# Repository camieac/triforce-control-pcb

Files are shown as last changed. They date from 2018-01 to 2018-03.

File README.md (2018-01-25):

# triforce-control-pcb

## Repository Navigation
This repository hosts the electronics hardware designs for the Triforce Fight Controller. Links to the main software repositories are below:

### [Triforce Control](https://github.com/TeamTriforceUK/triforce-control)

The Triforce Control firmware (mbed OS) runs on an LPC1768 (ARM Cortex M3). The firmware is responsible for controlling the robot.

### [Triforce Telemetry](https://github.com/TeamTriforceUK/triforce-telemetry)

The Triforce Telemetry repository hosts firmware (FreeRTOS) for the ESP8266 WiFi chip. This microcontroller works alongside the mbed to provide telemetry functionality via an HTTP server.

The ESP8266 allows us to communicate telemetry from Triforce to connected mobile devices (tablets, laptops, mobile phones). We also control non-safety critical settings such as LED lights from the mobile device.

## System Overview

### Microprocessors

| Device  | Firmware  | Language |
|---|---|---|
| [LPC1768](https://developer.mbed.org/platforms/mbed-LPC1768/) | [mbed OS](https://www.mbed.com/en/development/mbed-os/) | C++ |
| [ESP8266](https://www.adafruit.com/product/2471) | [FreeRTOS](http://www.freertos.org/)  | C |

### Sensors

| Sensor | Purpose | Communication |
|---|---|---|
| [BNO055](https://learn.adafruit.com/adafruit-bno055-absolute-orientation-sensor/overview) | Orientation, direction, acceleration |  I2C |

# PCB Spec

# Board Dimensions

| Width | Height | Thickness |
|---|---|---|
| 75mm  | 85mm | 1.6mm |

# Useful Links

## Enclosure

https://www.hammfg.com/files/parts/pdf/1455J1202.pdf
https://www.hammfg.com/part/1455J1202

## Generating gerber files

http://support.seeedstudio.com/knowledgebase/articles/1824574-how-to-generate-gerber-and-drill-files-from-kicad

## Contributing

We are open to any contributions in terms of ideas, suggestions, bug reports, development. Feel free to open GitHub issues regarding any contributions.

## Licensing

Licensed under CERN OHL v.1.2.

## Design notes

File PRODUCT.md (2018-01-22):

# PRODUCT.TXT

This file lists all known Triforce Fight Controller products that have been manufactured to date.
We are always interested in seeing our work being used by others.
We invite anyone who has made any of our boards to let us know and we will gladly add you to this list.

| Name | Team | Date (ISO 8601) | Version | Repository | Commit | Quantity | Purpose | Manufacturer |
|---|---|---|---|---|---|---|---|---|
| Cameron Craig | Team Triforce | 2018-01-19 | pre-release | github.com/camieac/triforce-control-pcb  | aeb3d275cbf074ca4e43f0d91900493fc6915f59 | 10 | Prototype | PCBWay |

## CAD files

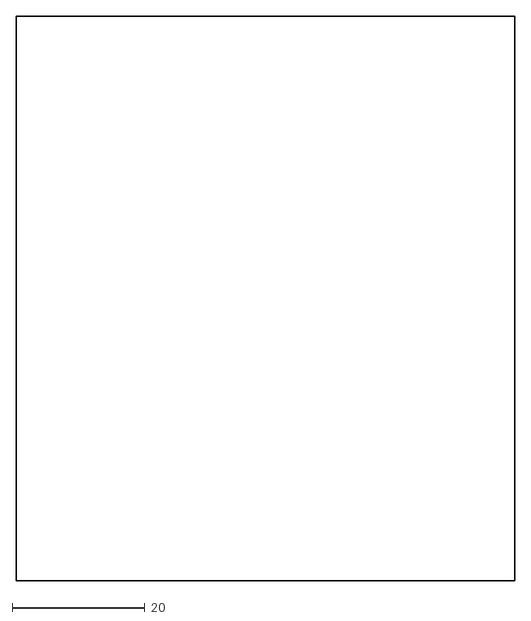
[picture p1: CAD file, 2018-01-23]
3d/drawings/board_outline2.dxf
75.0 x 85.0

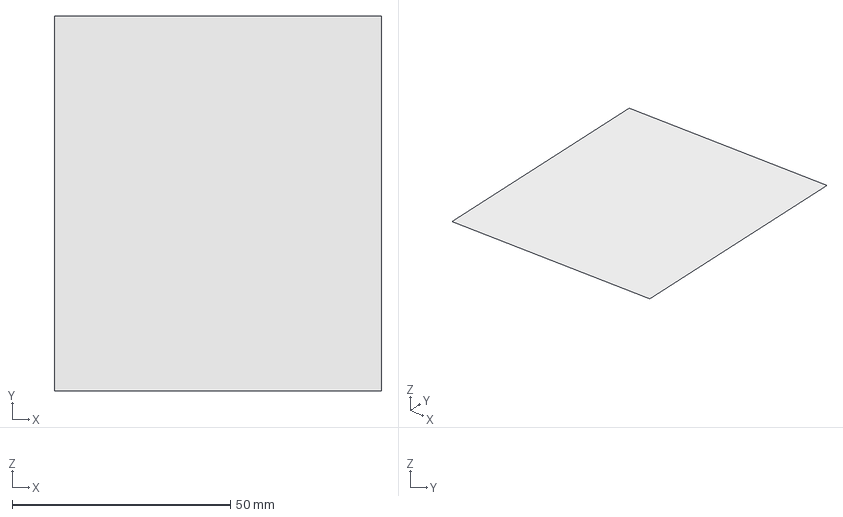
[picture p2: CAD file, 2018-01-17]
3d/drawings/board_outline.fcstd
75.0 x 86.0 x 0 mm

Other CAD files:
3d/drawings/board_outline.dxf

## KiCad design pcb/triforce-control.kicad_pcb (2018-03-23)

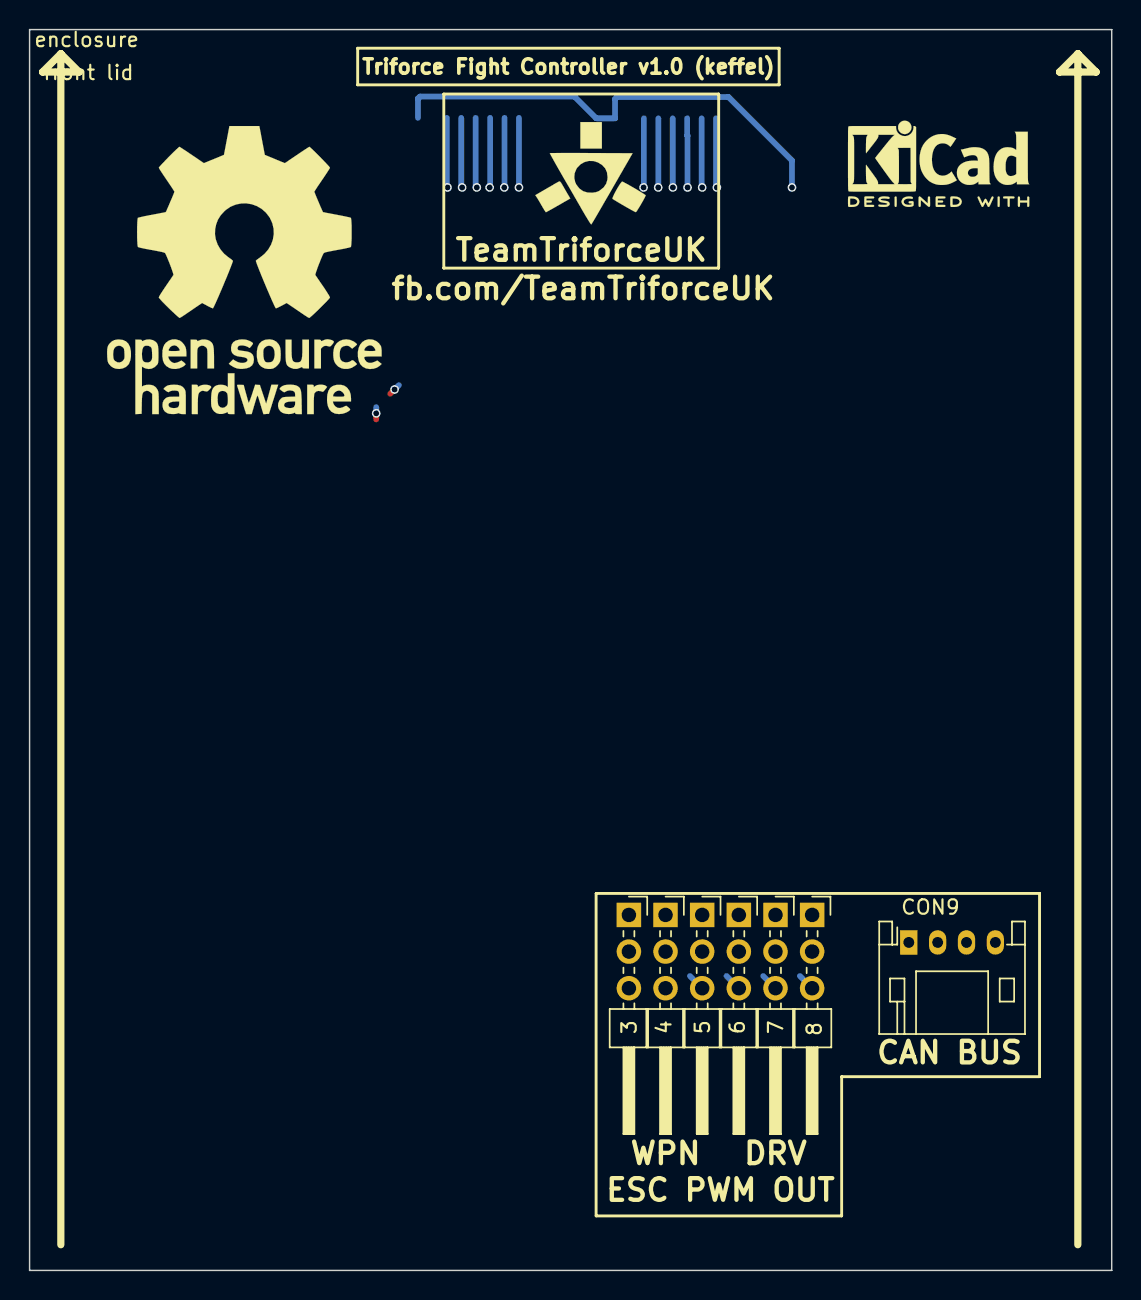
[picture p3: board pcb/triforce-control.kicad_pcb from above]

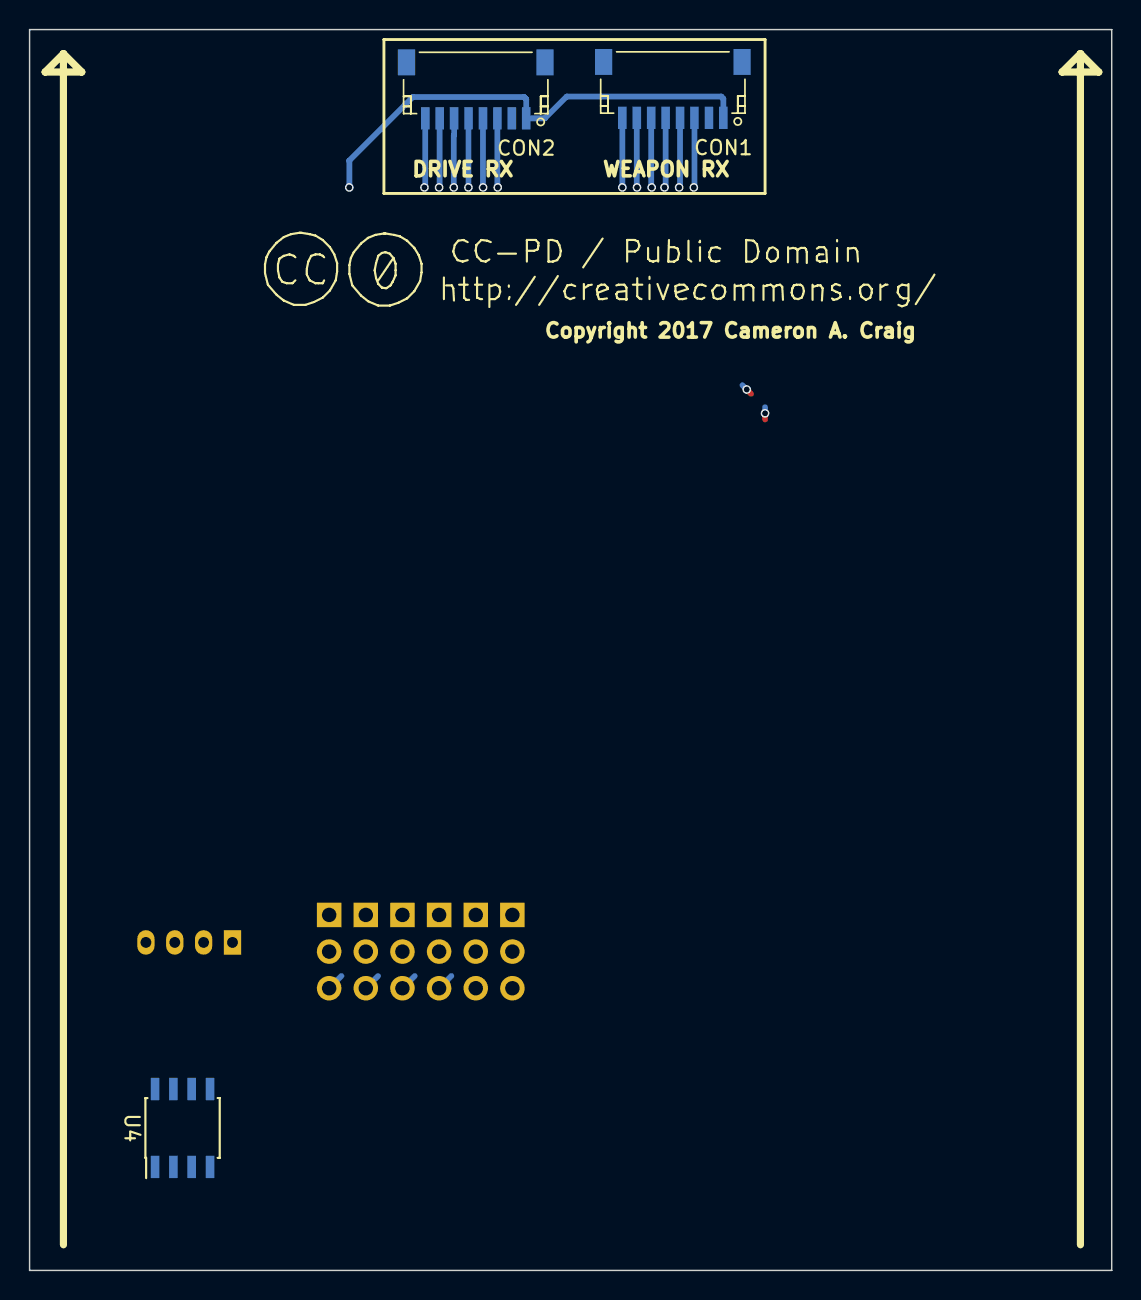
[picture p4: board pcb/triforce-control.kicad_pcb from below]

Board: 2 copper layers, 75.0 x 86.0 mm, 13 parts (3 on the bottom side), 4 nets.

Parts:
3: CON_ESC_W1; Pin_Header_Angled_3x01_Pitch2.54mm
4: CON_ESC_W2; Pin_Header_Angled_3x01_Pitch2.54mm
5: CON_ESC_W3; Pin_Header_Angled_3x01_Pitch2.54mm
6: CON_ESC_D1; Pin_Header_Angled_3x01_Pitch2.54mm
7: CON_ESC_D2; Pin_Header_Angled_3x01_Pitch2.54mm
8: CON_ESC_D3; Pin_Header_Angled_3x01_Pitch2.54mm
CON1, CON2: Conn_01x08; JST_SH_SM08B-SRSS-TB_08x1.00mm_Angled
CON9: Conn_01x04; JST_PH_S4B-PH-K_04x2.00mm_Angled
U4: SN65HVD232; SOIC-8_3.9x4.9mm_Pitch1.27mm
back lid: enclosure
enclosure: enclosure
front lid: enclosure

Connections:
+5V: 3.2, 4.2, 5.2, 6.2, 7.2, 8.2, CON1.2, CON2.2, CON9.4
CAN_H: CON9.3, U4.7
CAN_L: CON9.2, U4.6
GND: 3.1, 4.1, 5.1, 6.1, 7.1, 8.1, CON1.1, CON2.1, CON9.1, U4.2

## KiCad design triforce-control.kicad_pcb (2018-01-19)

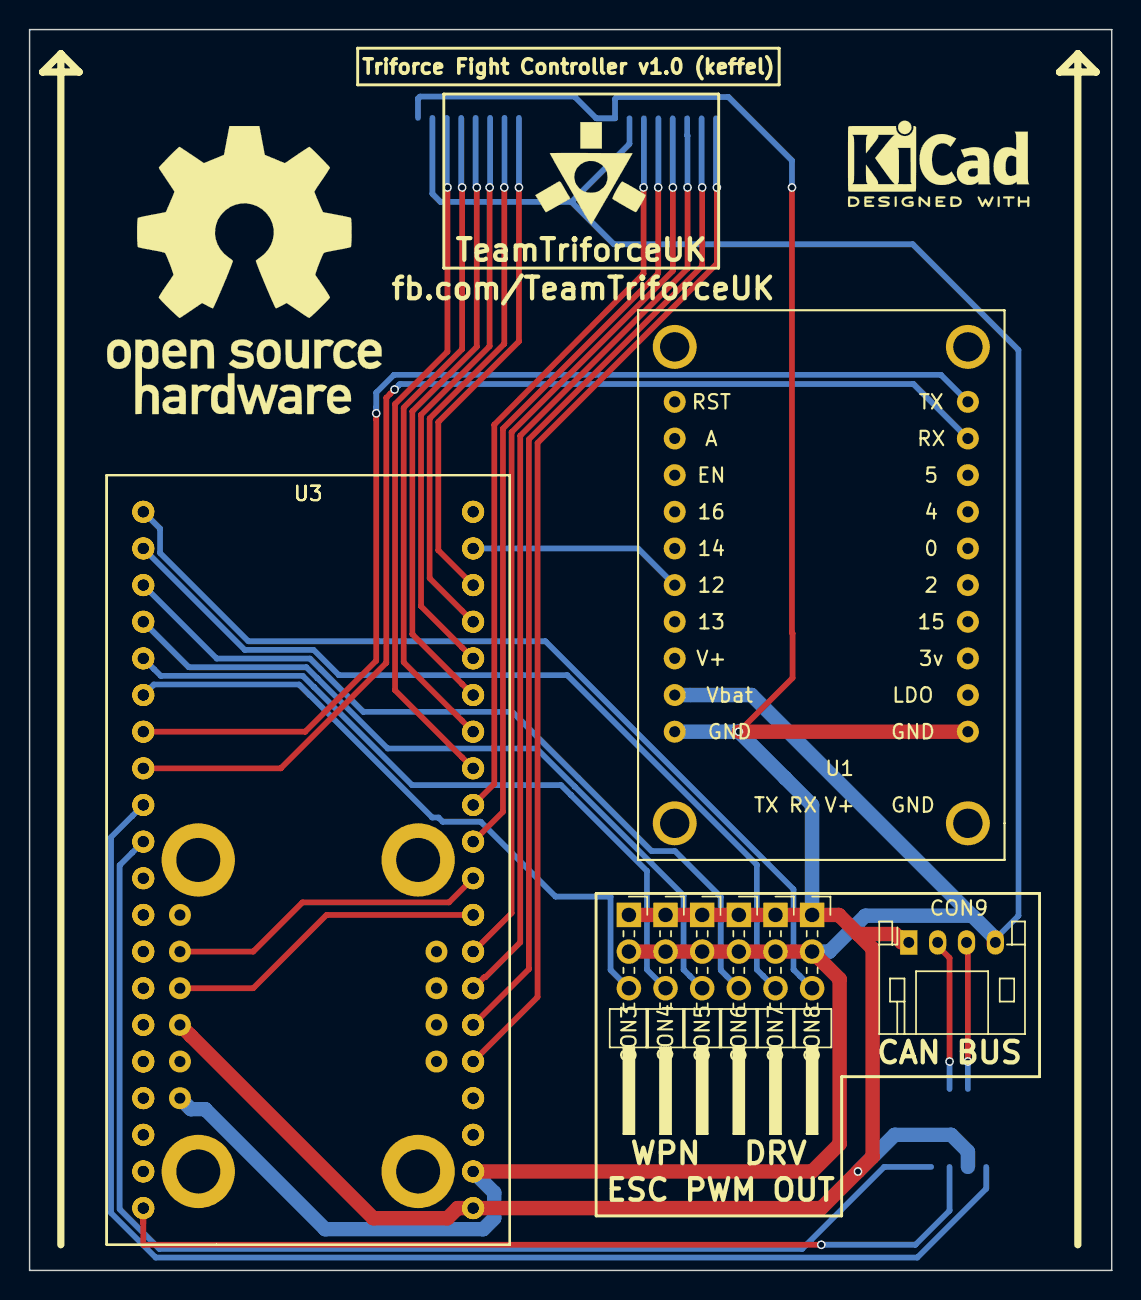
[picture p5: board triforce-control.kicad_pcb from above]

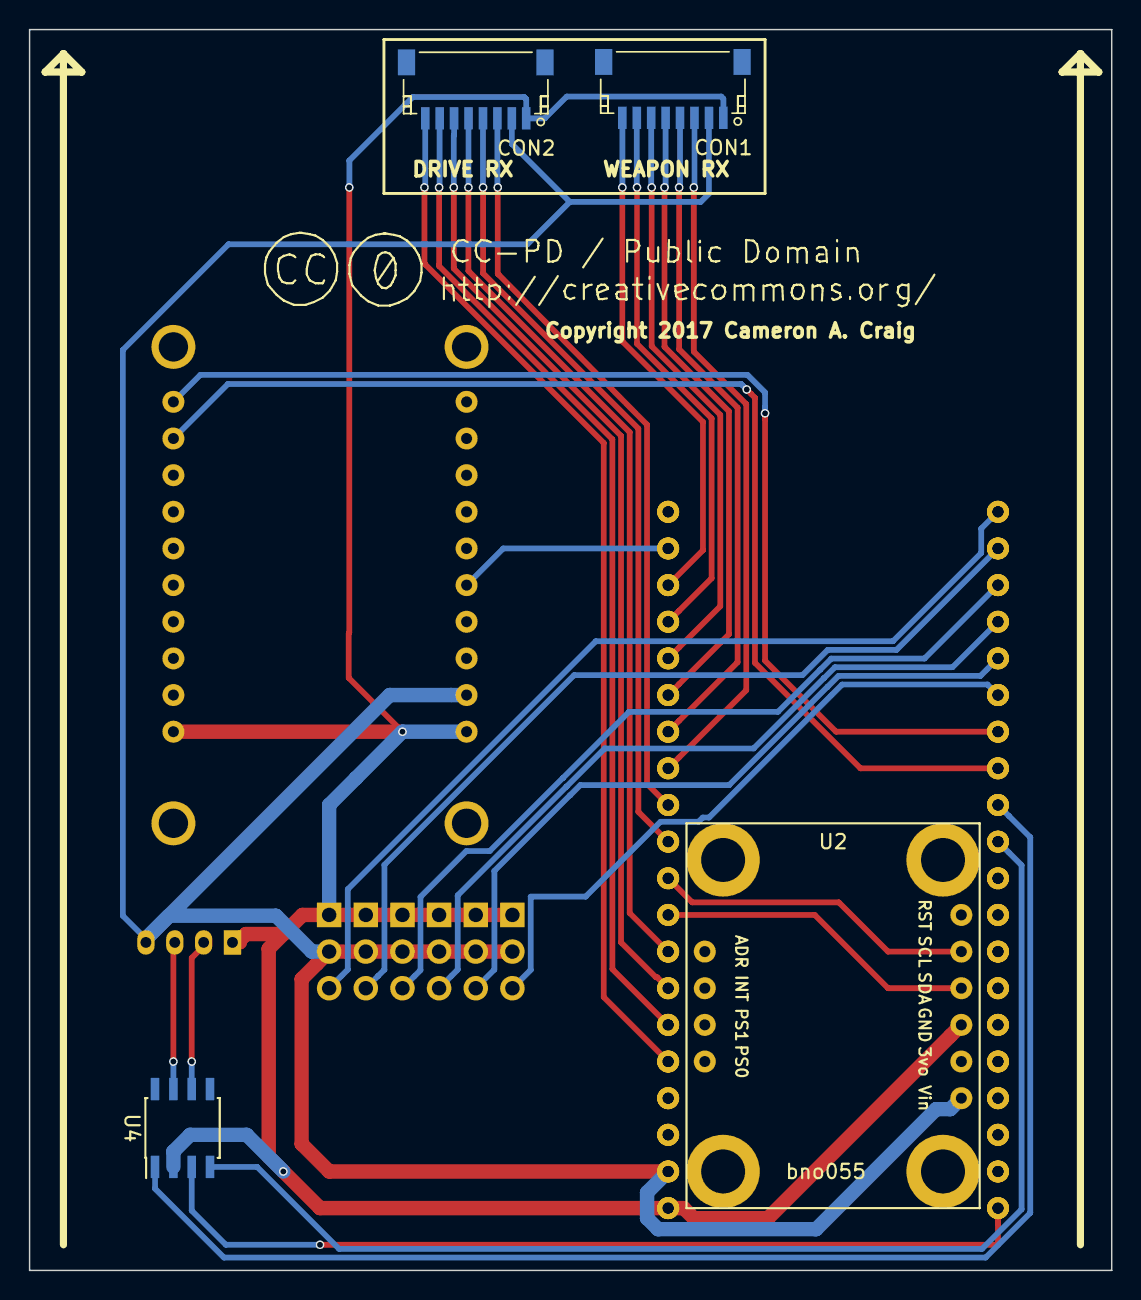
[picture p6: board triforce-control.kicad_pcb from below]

Board: 2 copper layers, 75.0 x 86.0 mm, 14 parts (4 on the bottom side), 42 nets.

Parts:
CON1, CON2: Conn_01x08; JST_SH_SM08B-SRSS-TB_08x1.00mm_Angled
CON3: CON_ESC_W1; Pin_Header_Angled_3x01_Pitch2.54mm
CON4: CON_ESC_W2; Pin_Header_Angled_3x01_Pitch2.54mm
CON5: CON_ESC_W3; Pin_Header_Angled_3x01_Pitch2.54mm
CON6: CON_ESC_D1; Pin_Header_Angled_3x01_Pitch2.54mm
CON7: CON_ESC_D2; Pin_Header_Angled_3x01_Pitch2.54mm
CON8: CON_ESC_D3; Pin_Header_Angled_3x01_Pitch2.54mm
CON9: Conn_01x04; JST_PH_S4B-PH-K_04x2.00mm_Angled
U1: ADAFRUIT_HUZZAH; ESP8266
U2: bno055; BNO055
U3, U3#2: LPC1768; lpc1768
U4: SN65HVD232; SOIC-8_3.9x4.9mm_Pitch1.27mm

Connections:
+5V: CON1.2, CON2.2, CON3.2, CON4.2, CON5.2, CON6.2, CON7.2, CON8.2, CON9.4, U1.9, U2.1, U3.2, U3#2.2
BNO_MBED_SCL: U2.5, U3.10, U3#2.10
BNO_MBED_SDA: U2.4, U3.9, U3#2.9
CAN_H: CON9.3, U4.7
CAN_L: CON9.2, U4.6
CAN_RXD: U3.30, U3#2.30, U4.4
CAN_TXD: U3.29, U3#2.29, U4.1
ESP_MBED_RX: U1.20, U3.27, U3#2.27
ESP_MBED_TX: U1.19, U3.28, U3#2.28
ESP_READY: U1.6, U3.19, U3#2.19
GND: CON1.1, CON2.1, CON3.1, CON4.1, CON5.1, CON6.1, CON7.1, CON8.1, CON9.1, U1.10, U1.11, U2.3, U3.1, U3#2.1, U4.2
IN_RX_D1: CON1.3, U3.13, U3#2.13
IN_RX_D2: CON1.4, U3.14, U3#2.14
IN_RX_D3: CON1.5, U3.15, U3#2.15
IN_RX_D4: CON1.6, U3.16, U3#2.16
IN_RX_D5: CON1.7, U3.17, U3#2.17
IN_RX_D6: CON1.8, U3.18, U3#2.18
IN_RX_W1: CON2.3, U3.12, U3#2.12
IN_RX_W2: CON2.4, U3.11, U3#2.11
IN_RX_W3: CON2.5, U3.8, U3#2.8
IN_RX_W4: CON2.6, U3.7, U3#2.7
IN_RX_W5: CON2.7, U3.6, U3#2.6
IN_RX_W6: CON2.8, U3.5, U3#2.5
MBED_3V3: U3.40, U3#2.40, U4.3
unnamed: U3.3, U3#2.3
unnamed: U3.4, U3#2.4
unnamed: U3.20, U3#2.20
unnamed: U3.31, U3#2.31
unnamed: U3.32, U3#2.32
unnamed: U3.33, U3#2.33
unnamed: U3.34, U3#2.34
unnamed: U3.35, U3#2.35
unnamed: U3.36, U3#2.36
unnamed: U3.37, U3#2.37
unnamed: U3.38, U3#2.38
unnamed: U3.39, U3#2.39
PWM_OUT_DRV_MOTOR_1: CON6.3, U3.23, U3#2.23
PWM_OUT_DRV_MOTOR_2: CON7.3, U3.22, U3#2.22
PWM_OUT_DRV_MOTOR_3: CON8.3, U3.21, U3#2.21
PWM_OUT_WPN_MOTOR_1: CON3.3, U3.26, U3#2.26
PWM_OUT_WPN_MOTOR_2: CON4.3, U3.25, U3#2.25
PWM_OUT_WPN_MOTOR_3: CON5.3, U3.24, U3#2.24

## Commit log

2017-12-20 Started new PCB design.
    [triforce-control.kicad_pcb, triforce-control.sch]
2017-12-21 Added JST and enclosure datasheets.
2017-12-21 Added missing GND connection.
    [triforce-control.kicad_pcb]
2017-12-23 Prettifying the front silkscreen with symbols and text.
    [triforce-control.kicad_pcb]
2018-01-13 Changed tracks.
    [triforce-control.kicad_pcb]
2018-01-14 Swapped JSP PH for JST SH on RX inputs.
    [triforce-control.kicad_pcb, triforce-control.sch]
2018-01-16 Added JST SH 3D model.
    [triforce-control.kicad_pcb]
2018-01-17 Added Triforce logo and JST SH models.
    [triforce-control.kicad_pcb]
2018-01-17 Added outline as DXF.
    [board_outline.dxf, board_outline.fcstd, triforce-control.kicad_pcb]
2018-01-17 Moved some tracks.
    [triforce-control.kicad_pcb]
2018-01-19 Connected an extra ESP8266 ground pin.
    [triforce-control.sch]
2018-01-19 Updated netlist with new ground connection.
2018-01-19 Added silkscreen art.
    [triforce-control.kicad_pcb]
2018-01-19 Added boundary boxes on silkscreen for connector blocks.
    [triforce-control.kicad_pcb]
2018-01-19 PCB track cleanup and alignment.
    [triforce-control.kicad_pcb]
2018-01-23 Moved PCB to pcb folder.
    [triforce-control.kicad_pcb]
2018-01-23 Started moving component source files to external repository.
    [triforce-control.kicad_pcb]
2018-01-23 Moved schematics to schematics folder.
    [fight-controller-main.sch, fight-controller-schematics.sch]
2018-01-23 Added folder for manufacturing files.
    [triforce-control-B.Cu.gbl, triforce-control-B.Mask.gbs, triforce-control-B.SilkS.gbo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]
2018-01-23 Added board outline drawing.
    [board_outline2.dxf]
2018-01-23 Started adding enclosure parts as footprints.
    [triforce-control.kicad_pcb]
2018-01-25 Added enclosure 3d shapes to PCB.
    [triforce-control.kicad_pcb]
2018-01-25 Removed old schematic.
    [triforce-control.sch]
2018-01-25 Removed old PCB file.
2018-01-25 Updated schematics to use components lib.
2018-03-23 Started v2.x work, integrating developement boards into PCB.
    [connections.sch, esp.sch, esp8266.sch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]

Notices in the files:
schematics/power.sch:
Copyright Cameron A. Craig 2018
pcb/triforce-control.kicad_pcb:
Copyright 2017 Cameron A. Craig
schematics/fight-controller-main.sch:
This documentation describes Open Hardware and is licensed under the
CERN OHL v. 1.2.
